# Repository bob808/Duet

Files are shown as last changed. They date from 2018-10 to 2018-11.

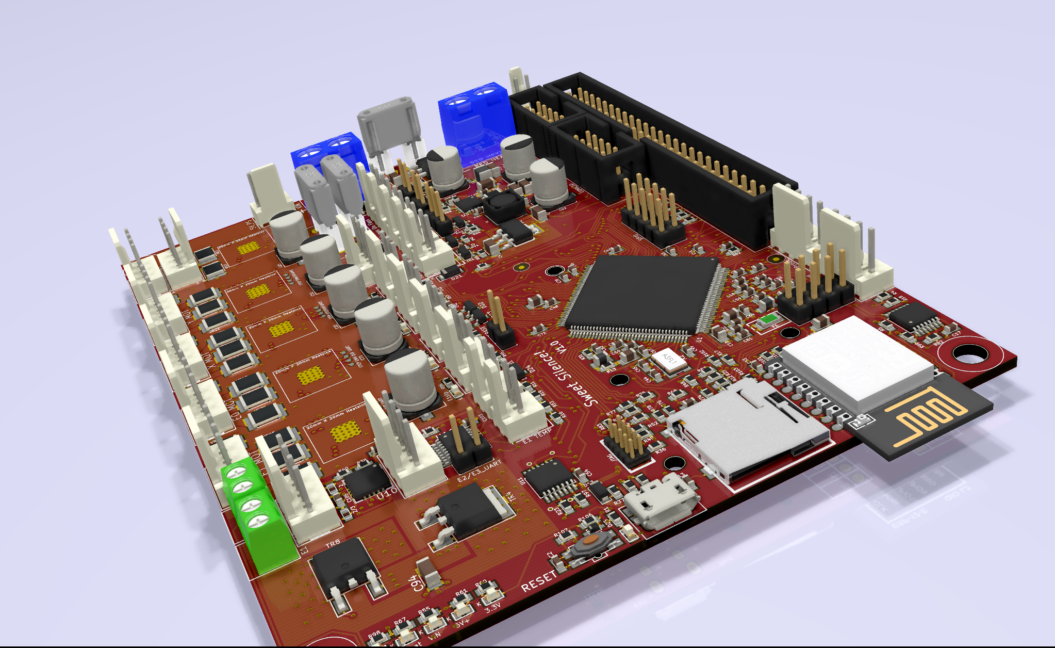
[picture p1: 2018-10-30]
top w:o radiators.png

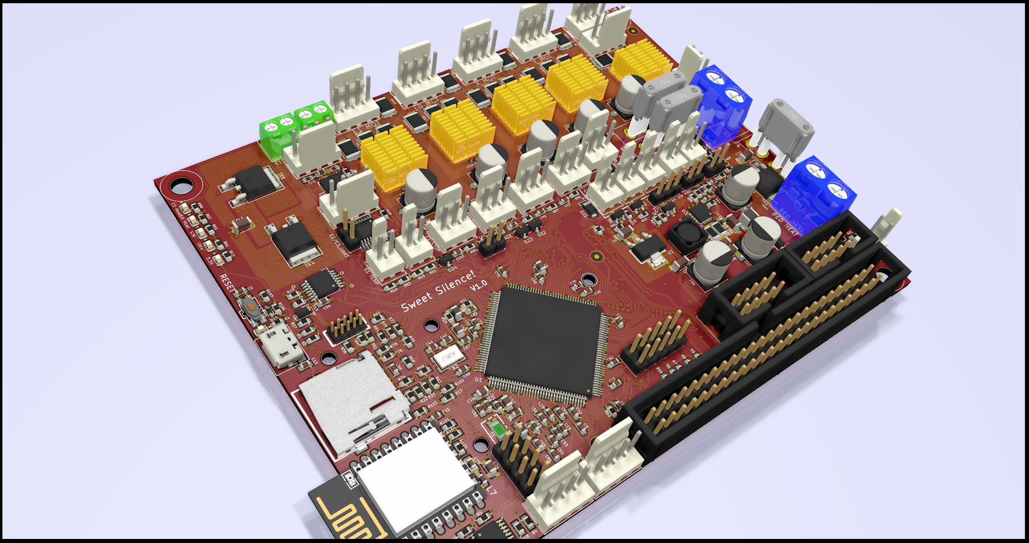
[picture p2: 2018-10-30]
top with radiators.png

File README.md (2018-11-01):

# The Sweet Silence! 3D Printer Controller design files repository.

Sweeet Silence is a Duet2 Wifi spinoff, using tmc2228 drivers, mounted on the back of the pcb for better 
cooling (heatsinks on top pf pcb). Uses the same ATSAM4E8E processor. Output stage has been completely redone,
and includes full protection suite from the datasheet (ferrite beads/varistors and caps on BRA/BRB).
You can skip the varistors, drivers work fine without them.
There's 2x MAX31865 chips on board, you can use it directly with PT100/1000 sensors. There's also options
for 4/3/2 wire setups.
The driver control should be the same from Maestro.
There's E2/E3 extra UART connections for external drivers.
Few pins from 2x25 header are different, and debugging led is gone. Everything else should be the same.

Will update later on with more details. I found all parts at TME/Farnell. 
Firmware needs to be modified to account for correct pin numbers.
Ah, and max31865 is to be bitbanged. No hardware SPI in that area.

The recommended firmware is DC42's branch of the RepRapFirmware:
https://github.com/dc42/RepRapFirmware

Based on :
Duet 2 Wifi 
Design by Tony Lock and David Crocker
More info:
https://www.duet3d.com/
LICENSE: see the LICENSE file in the repository

Developed in KiCAD: http://www.kicad-pcb.org/display/KICAD/KiCad+EDA+Software+Suite

top with radiators
top w o radiators
bottom

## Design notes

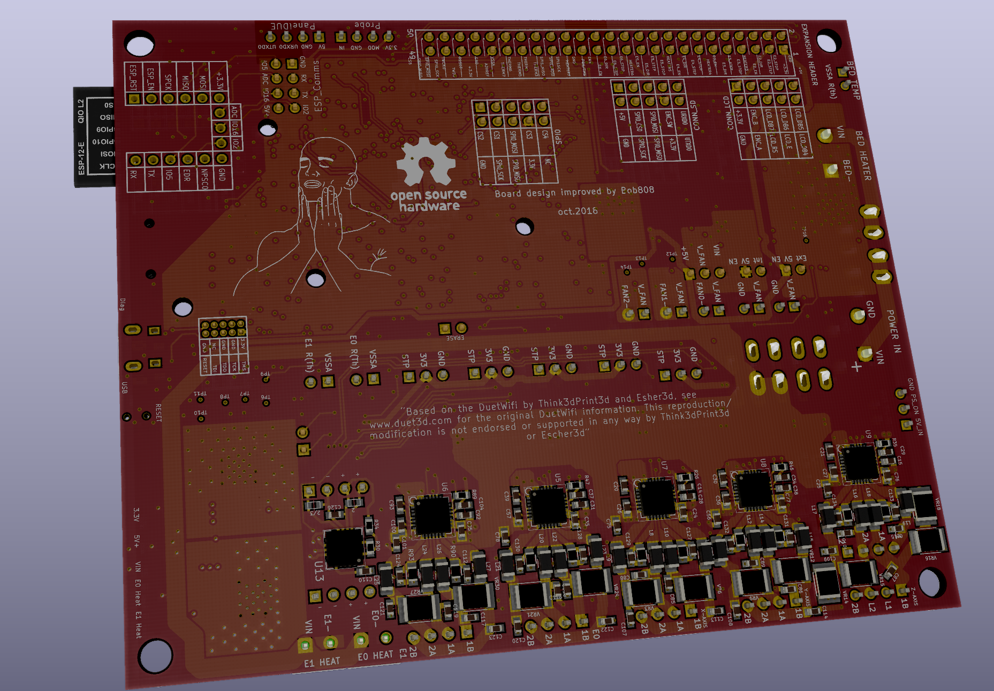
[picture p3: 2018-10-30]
bottom.png

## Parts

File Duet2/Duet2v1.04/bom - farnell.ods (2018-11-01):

Order Code | Quantity | Mfg. Code | Mfg Name | Description
2515574 | 2 | MAX31865ATP+ | MAXIM INTEGRATED PRODUCTS | MAXIM INTEGRATED PRODUCTS Temperature Sensor IC, RTD, Digital, ± 0.5°C, -40 °C, 125 °C, TQFN, 20 Pins
1669752 | 10 | MPZ2012S221A | TDK | TDK Ferrite Bead, 0805 [2012 Metric], 220 ohm, 3 A, MPZ Series, 0.04 ohm, ± 25%
2822172 | 5 | TMC2224-LA-T | TRINAMIC | TRINAMIC Motor Driver/Controller, Stepper, UART, 1 Output, 4.75 V to 36 V Supply, 1.4 A Out, QFN-28
2496341 | 1 | SN74CB3Q3251PWR | TEXAS INSTRUMENTS | TEXAS INSTRUMENTS Multiplexer / Demultiplexer Bus Switch, CB3Q Family, 1 Channels, 1:8, 2.3 V to 3.6 V, TSSOP-16
7261403 | 1 | TS2940CW-3.3 RP | TAIWAN SEMICONDUCTOR | TAIWAN SEMICONDUCTOR Fixed LDO Voltage Regulator, 0V to 35V, 600mV Dropout, 3.3Vout, 1Aout, SOT-223-3
2292371 | 20 | HI1206T500R-10 | LAIRD | LAIRD Ferrite Bead, 1206 [3216 Metric], 50 ohm, 6 A, HI Series, 0.01 ohm
2292537 | 1 | TYS6045100M-10 | LAIRD | LAIRD Power Inductor (SMD), 10 µH, 2.45 A, Shielded, 3.2 A, TYS Series, 6mm x 6mm x 4.5mm
2534550 | 1 | 74479299210 | WURTH ELEKTRONIK | WURTH ELEKTRONIK Power Inductor (SMD), 1 µH, Shielded, 5.2 A, WE-PMCI Series, 1210 [3225 Metric]
2834883 | 1 | 0ZCJ0020FF2E | BEL FUSE - CIRCUIT PROTECTION | BEL FUSE - CIRCUIT PROTECTION PPTC Resettable Fuse, SMD, 0ZCJ Series, 200 mA, 400 mA, 30 VDC, -40 °C
2889217 | 5 | SL04-HE3-08 | VISHAY | VISHAY Schottky Rectifier, 40 V, 1.1 A, Single, DO-219AB, 2 Pins, 540 mV
2504957 | 3 | ACPP06034K7BE | ARCOL | ARCOL SMD Chip Resistor, Precision Passivated, 4.7 kohm, ACPP Series, 50 V, Thin Film, 0603 [1608 Metric]
2861442 | 10 | CRGCQ0603F27R | TE CONNECTIVITY | TE CONNECTIVITY SMD Chip Resistor, 27 ohm, CRGCQ Series, 75 V, Thick Film, 0603 [1608 Metric], 100 mW
1081192 | 5 | BAT54C,215 | NEXPERIA | NEXPERIA Small Signal Schottky Diode, Dual Common Cathode, 30 V, 200 mA, 800 mV, 600 mA, 150 °C
2116426 | 10 | RLP73K2BR12JTD | TE CONNECTIVITY | TE CONNECTIVITY SMD Current Sense Resistor, 0.12 ohm, RL73 Series, 1206 [3216 Metric], 500 mW, ± 5%, Thick Film
2908248 | 30 | CR0603-FX-1002GLF | BOURNS | BOURNS SMD Chip Resistor, 10 kohm, CR Series, 50 V, Thick Film, 0603 [1608 Metric], 100 mW
2861477 | 10 | CRGCQ0603F22K | TE CONNECTIVITY | TE CONNECTIVITY SMD Chip Resistor, 22 kohm, CRGCQ Series, 75 V, Thick Film, 0603 [1608 Metric], 100 mW
2074166 | 10 | MCSR06X1001FTL | MULTICOMP | MULTICOMP SMD Chip Resistor, 1 kohm, MCSR 06 Series, 75 V, Ceramic, 0603 [1608 Metric], 100 mW
2447363 | 10 | MCWR06X3901FTL | MULTICOMP | MULTICOMP SMD Chip Resistor, 3.9 kohm, MCWR Series, 50 V, Thick Film, 0603 [1608 Metric], 100 mW
2861497 | 10 | CRGCQ0603F1M0 | TE CONNECTIVITY | TE CONNECTIVITY SMD Chip Resistor, 1 Mohm, CRGCQ Series, 75 V, Thick Film, 0603 [1608 Metric], 100 mW
2496924 | 20 | 0603X225K6R3CT | WALSIN | WALSIN SMD Multilayer Ceramic Capacitor, 2.2 µF, 6.3 V, 0603 [1608 Metric], ± 10%, X5R
2896440 | 10 | VJ0603Y223KXACW1BC | VISHAY | VISHAY SMD Multilayer Ceramic Capacitor, 22000 pF, 50 V, 0603 [1608 Metric], ± 10%, X7R, VJ Series
2896419 | 10 | VJ0603Y103KXAPW1BC | VISHAY | VISHAY SMD Multilayer Ceramic Capacitor, 10000 pF, 50 V, 0603 [1608 Metric], ± 10%, X7R, VJ Series
2362105 | 5 | GRM21BR60J106KE01L | MURATA | MURATA SMD Multilayer Ceramic Capacitor, 10 µF, 6.3 V, 0805 [2012 Metric], ± 10%, X5R, GRM Series
2112852 | 5 | LMK212B7475KG-T | TAIYO YUDEN | TAIYO YUDEN SMD Multilayer Ceramic Capacitor, 4.7 µF, 10 V, 0805 [2012 Metric], ± 10%, X7R, M Series
2611949 | 10 | GRM319R6YA106KA12D | MURATA | MURATA SMD Multilayer Ceramic Capacitor, 10 µF, 35 V, 1206 [3216 Metric], ± 10%, X5R, GRM Series
1868417 | 7 | EEEFT1V101AP | PANASONIC ELECTRONIC COMPONENTS | PANASONIC ELECTRONIC COMPONENTS SMD Aluminium Electrolytic Capacitor, Radial Can - SMD, 100 µF, 35 V, 0.26 ohm, FT Series
2861485 | 10 | CRGCQ0603F100K | TE CONNECTIVITY | TE CONNECTIVITY SMD Chip Resistor, 100 kohm, CRGCQ Series, 75 V, Thick Film, 0603 [1608 Metric], 100 mW
2447385 | 10 | MCWR06X4701FTL | MULTICOMP | MULTICOMP SMD Chip Resistor, 4.7 kohm, MCWR Series, 50 V, Thick Film, 0603 [1608 Metric], 100 mW
2078911 | 10 | ASC0603-2K2FT5 | TT ELECTRONICS / WELWYN | TT ELECTRONICS / WELWYN SMD Chip Resistor, 2.2 kohm, ASC Series, 50 V, Thick Film, 0603 [1608 Metric], 100 mW
2074202 | 10 | MCSR06X1800FTL | MULTICOMP | MULTICOMP SMD Chip Resistor, 180 ohm, MCSR 06 Series, 75 V, Ceramic, 0603 [1608 Metric], 100 mW
2447419 | 10 | MCWR06X6800FTL | MULTICOMP | MULTICOMP SMD Chip Resistor, 680 ohm, MCWR Series, 50 V, Thick Film, 0603 [1608 Metric], 100 mW
2447362 | 10 | MCWR06X3601FTL | MULTICOMP | MULTICOMP SMD Chip Resistor, 3.6 kohm, MCWR Series, 50 V, Thick Film, 0603 [1608 Metric], 100 mW
2861481 | 10 | CRGCQ0603F47K | TE CONNECTIVITY | TE CONNECTIVITY SMD Chip Resistor, 47 kohm, CRGCQ Series, 75 V, Thick Film, 0603 [1608 Metric], 100 mW
2447227 | 10 | MCWR06X1000FTL | MULTICOMP | MULTICOMP SMD Chip Resistor, 100 ohm, MCWR Series, 50 V, Thick Film, 0603 [1608 Metric], 100 mW
2447298 | 10 | MCWR06X2200FTL | MULTICOMP | MULTICOMP SMD Chip Resistor, 220 ohm, MCWR Series, 50 V, Thick Film, 0603 [1608 Metric], 100 mW
2078905 | 10 | ASC0603-470RFT5 | TT ELECTRONICS / WELWYN | TT ELECTRONICS / WELWYN SMD Chip Resistor, 470 ohm, ASC Series, 50 V, Thick Film, 0603 [1608 Metric], 100 mW
2073453 | 10 | MCMR06X2702FTL | MULTICOMP | MULTICOMP SMD Chip Resistor, Ceramic, 27 kohm, MCMR Series, 75 V, Thick Film, 0603 [1608 Metric], 100 mW
2861445 | 10 | CRGCQ0603F47R | TE CONNECTIVITY | TE CONNECTIVITY SMD Chip Resistor, 47 ohm, CRGCQ Series, 75 V, Thick Film, 0603 [1608 Metric], 100 mW
2078888 | 10 | ASC0603-1R0FT5 | TT ELECTRONICS / WELWYN | TT ELECTRONICS / WELWYN SMD Chip Resistor, 1 ohm, ASC Series, 50 V, Thick Film, 0603 [1608 Metric], 100 mW
2812361 | 20 | 885012206106 | WURTH ELEKTRONIK | WURTH ELEKTRONIK SMD Multilayer Ceramic Capacitor, 470 pF, 100 V, 0603 [1608 Metric], ± 10%, X7R, WCAP-CSGP Series
2896437 | 10 | VJ0603Y222JXACW1BC | VISHAY | VISHAY SMD Multilayer Ceramic Capacitor, 2200 pF, 50 V, 0603 [1608 Metric], ± 5%, X7R, VJ Series
2896423 | 60 | VJ0603Y104JXACW1BC | VISHAY | VISHAY SMD Multilayer Ceramic Capacitor, 0.1 µF, 50 V, 0603 [1608 Metric], ± 5%, X7R, VJ Series
2066899 | 2 | 744760410A | WURTH ELEKTRONIK | WURTH ELEKTRONIK Surface Mount High Frequency Inductor, WE-RFI Series, 10 µH, 80 mA, 0805 [2012 Metric], Wirewound
1675756 | 50 | MC34485 | MULTICOMP | MULTICOMP Connector Housing, MC34 Series, Receptacle, 4 Ways, 2.54 mm, 2218T Crimp Contacts, Yes
1675755 | 50 | MC34483 | MULTICOMP | MULTICOMP Connector Housing, MC34 Series, Receptacle, 3 Ways, 2.54 mm, 2218T Crimp Contacts, Yes
1675754 | 50 | MC34481 | MULTICOMP | MULTICOMP Connector Housing, MC34 Series, Receptacle, 2 Ways, 2.54 mm, 2218T Crimp Contacts, Yes
1675764 | 50 | MC34629 | MULTICOMP | MULTICOMP Wire-To-Board Connector, Vertical, 2.54 mm, 2 Contacts, Header, MC34 Series, Through Hole, 1 Rows
1860642 | 100 | MC346772 | MULTICOMP | MULTICOMP Contact, Socket, Crimp, 18 AWG, Tin Plated Contacts, Multicomp's 4.2mm Housings
1748753 | 1 | 744761047C | WURTH ELEKTRONIK | WURTH ELEKTRONIK Surface Mount High Frequency Inductor, WE-KI Series, 4.7 nH, 700 mA, 0603 [1608 Metric], Wirewound
2554980 | 1 | ZX62D-B-5P8(30) | HIROSE(HRS) | HIROSE(HRS) USB Connector, Micro USB Type B, USB 2.0, Receptacle, 5 Ways, Surface Mount, Through Hole Mount
2696554 | 10 | UCR10EVHFSR075 | ROHM | ROHM SMD Current Sense Resistor, 0.075 ohm, UCR Series, 0805 [2012 Metric], 330 mW, ± 1%, Thick Film

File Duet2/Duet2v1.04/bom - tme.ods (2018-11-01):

Symbol | Manufacturer part number | Producer | Quantity
PMV40UN2R | PMV40UN2R | NEXPERIA | 5
ZL231-50PG | DS1013-50SSIB1 | CONNFLY | 1
DS1017-01-10NA8 | DS1017-01-10NA8 | CONNFLY | 1
IPD040N03LGATMA1 | IPD040N03LGATMA1 | INFINEON TECHNOLOGIES | 5
UCV1V221MCL1GS | UCV1V221MCL1GS | NICHICON | 1
A4403GEUTR-T | A4403GEUTR-T | ALLEGRO MICROSYSTEMS | 1
SN74HC74PW | SN74HC74PW | TEXAS INSTRUMENTS | 3
SN74HCT02PW | SN74HCT02PW | TEXAS INSTRUMENTS | 3
ATSAM4E8EA-AN | ATSAM4E8EA-AN | MICROCHIP TECHNOLOGY | 1
KEYS3522 | 3522 | KEYSTONE | 10
0ZCJ0020FF2E | 0ZCJ0020FF2E | BEL FUSE | 1
B72580V250K62 | B72580V250K62 | EPCOS | 30
MCC-SDMICRO/3 | 112J-TDAR-R01 | ATTEND | 1
MX-105017-0001 | 105017-0001 | MOLEX | 2
KMR223GLFG | Y78B22310FP | C&K | 1
KMS233GLFG | Y28B23310FP | C&K | 1
20021111-00010T4LF | 20021111-00010T4LF | AMPHENOL | 2
MKDS5/2-6.35 | MKDS 5/ 2-6 | 35 1714955 PHOENIX CONTACT | 2
TB-3.5-P-2P-GY | TB-3.5-P-2P-GY | NINIGI | 2
NS25-W3P | NS25-W3P | NINIGI | 10
MX-22-23-2041 | 22-23-2041 | MOLEX | 10
OSR50603C1E | OSR50603C1E | OPTOSUPPLY | 10
OSO50603C1E | OSO50603C1E | OPTOSUPPLY | 10
OSG80603C1E | OSG80603C1E | OPTOSUPPLY | 10
RB751S40.115 | RB751S40.115 | NEXPERIA | 10
SS14M | SS14M RS | TAIWAN SEMICONDUCTOR | 5
SKL33-DIO | SKL33 | DIOTEC SEMICONDUCTOR | 5
OSM50603C1E | OSM50603C1E | OPTOSUPPLY | 5
1-826632-0 | 1-826632-0 | TE CONNECTIVITY | 1
826629-6 | 826629-6 | TE CONNECTIVITY | 3
75869-301LF | 75869-301LF | AMPHENOL | 2
ISM92-3351AH12.00 | ISM92-3351AH-12.0000 | ILSI | 1

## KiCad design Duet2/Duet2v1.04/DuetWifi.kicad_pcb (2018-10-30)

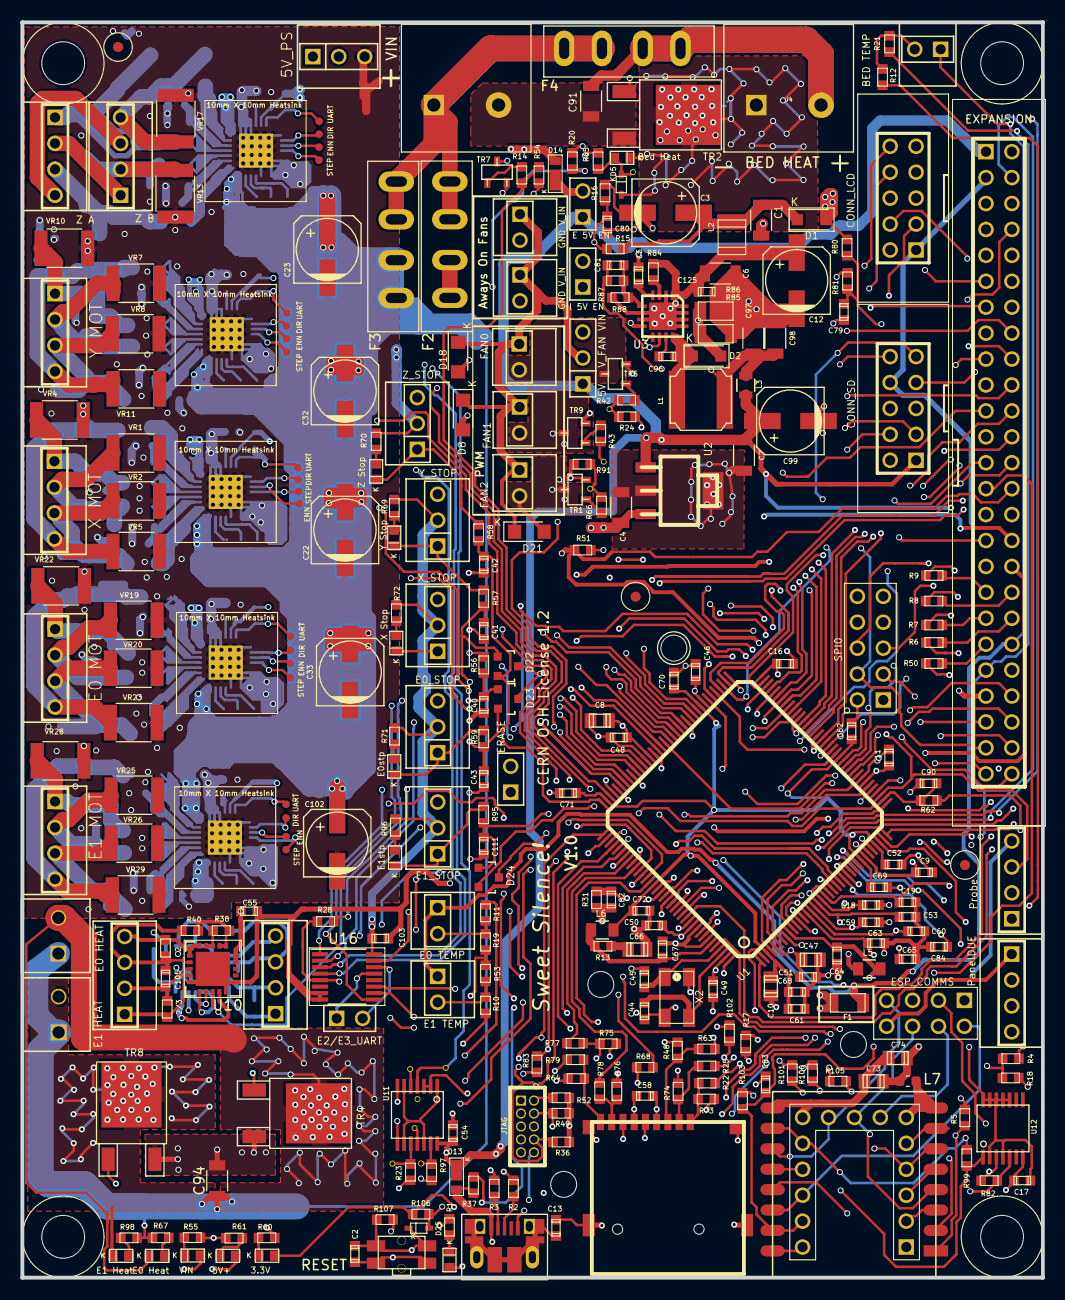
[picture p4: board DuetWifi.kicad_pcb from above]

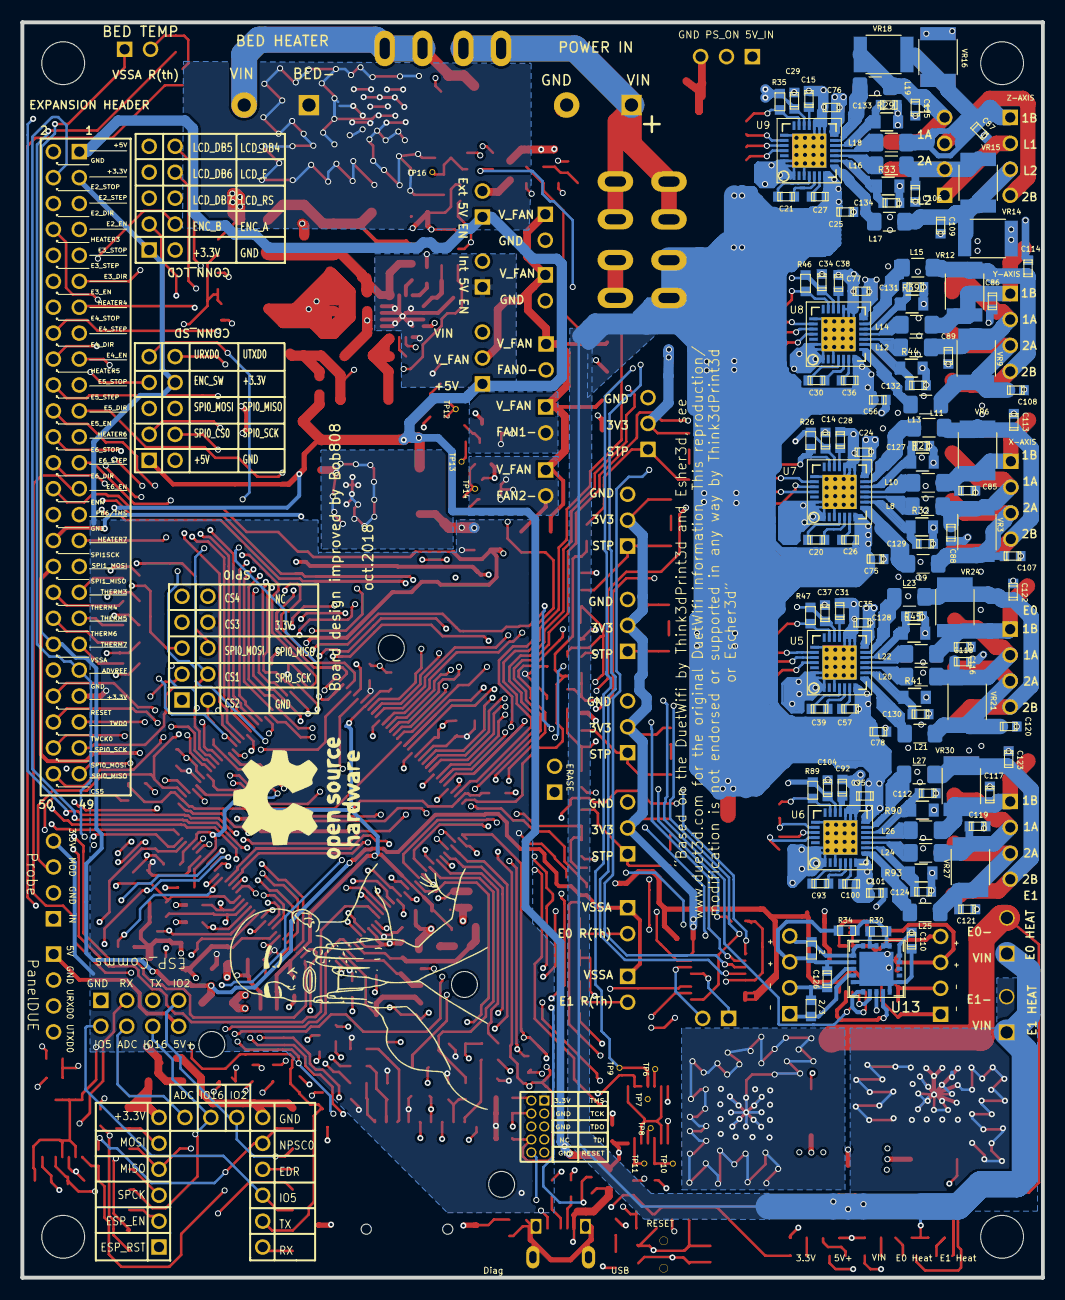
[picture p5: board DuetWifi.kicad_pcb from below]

Board: 4 copper layers, 100.0 x 123.0 mm, 430 parts (120 on the bottom side), 305 nets.

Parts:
C1, C4, C6, C7, C91, C94, C97, C98: 10u 35V; C_1206
C2, C13, C79, C80, C81: 0u01; C_0603
C3, C12, C22, C23, C32, C33, C102: 100u 35V; C_ELEC_6.3x7.7
C5, C9, C11, C16, C17, C29, C34, C37, C46, C48, C49, C50, C51, C52, C54, C61, C62, C64, C67, C69, C70, C71, C72, C82, C103, C104: 0u1; C_0603
C8, C10, C47, C73, C74: 10u; C_0805
C14, C24, C25, C35, C56, C75, C76, C77, C78, C95, C101: 0u1 50V; C_0603
C15, C18, C19, C28, C31, C38, C53, C58, C59, C60, C63, C65, C68, C84, C92: 2u2; C_0603
C20, C21, C30, C39, C93: 22n X7R 10% 16V; C_0603
C26, C27, C36, C57, C100: 0.1u 50V; C_0603
C40, C41, C42, C43, C55, C90, C110, C111: 2n2; C_0603
C44, C45: 10p; C_0603
C66: 4u7; C_0805
C83: DNP 47p; C_0603
C85, C86, C87, C88, C89, C106, C107, C108, C109, C113, C114, C115, C116, C117, C118, C119, C120, C121, C122, C123: 470p 100V; C_0603
C96: 22nF; C_0603
C99: 220u 25V; C_ELEC_6.3x7.7
C105, C126: 10n/100n; C_0603
C112, C124, C127, C128, C129, C130, C131, C132, C133, C134: 0u1 16V; C_0603
C125: 0u1 35V; C_0603
D1, D2: DB2W40300L; D_SOD-123F
D3: USB; D_0603
D5, D25: SOD-523F
D6: Bed Heat; D_0603
D7: E0 Heat; D_0603
D8, D18, D21: DO-219AB
D9: Y Stop; D_0603
D10: Z Stop; D_0603
D11: E0stp; D_0603
D12: X Stop; D_0603
D13, D14: SS14M; uSMA
D15: VIN; D_0603
D16: 3.3V; D_0603
D17: 5V+; D_0603
D19: E1stp; D_0603
D20: E1 Heat; D_0603
D22, D23, D24: BAT54C; SOT-23-D
F1: PPTC Resettable Fuse; R_1206
F2: FAN FUSE; MCCQ-122-minibladefuseholder
F3: EXT/STEP FUSE; MCCQ-122-minibladefuseholder
F4: BED FUSE; MCCQ-122-minibladefuseholder
J1: EXPANSION; PIN_ARRAY_25X2
J2: FAN2; PIN_ARRAY_2X1
J3: 5V V_FAN VIN; CONN_3x1
J4: BED HEAT; TERM_2-WAY_6.35mm
J5: BED TEMP; PIN_ARRAY_2X1
J6: E1 MOT; PIN_ARRAY_4x1
J7: Z B; PIN_ARRAY_4x1
J8: Y MOT; PIN_ARRAY_4x1
J9: X MOT; PIN_ARRAY_4x1
J10: E0 MOT; PIN_ARRAY_4x1
J11: E0 HEAT; 3.5MM_2X1
J12: E0 TEMP; PIN_ARRAY_2X1
J13: E1 HEAT; 3.5MM_2X1
J14: E1 TEMP; PIN_ARRAY_2X1
J15: uSDHC; uSD_SKT
J16: CONN_ALT_HEADER
J17, J18: + + - -; PIN_ARRAY_4x1
J19: Z_STOP; PIN_ARRAY_3X1
J20: 5V_PS; PIN_ARRAY_3X1
J21: JTAG; MICRO_5x2
J22: USB; uUSB_new
J23: VIN; TERM_2-WAY_6.35mm
J24, J31: GND V_IN; PIN_ARRAY_2X1
J25: FAN0; PIN_ARRAY_2X1
J26: E2/E3_UART; PIN_ARRAY_2X1_mod
J27, J42, J46, J50, J54: UART; tp_smd
J28: Probe; PIN_ARRAY_4x1
J29: FAN1; PIN_ARRAY_2X1
J30: PanelDUE; PIN_ARRAY_4x1
J32: Y_STOP; PIN_ARRAY_3X1
J33: X_STOP; PIN_ARRAY_3X1
J34: E0_STOP; PIN_ARRAY_3X1
J35: E1_STOP; PIN_ARRAY_3X1
J36: Z A; PIN_ARRAY_4x1
J37: SPI0; MAX_TEMP_DB
J38, J43, J47, J51, J55: ENN; tp_smd
J39: ESP_COMMS; CONN_4x2
J40, J44, J48, J52, J56: DIR; tp_smd
J41, J45, J49, J53, J57: STEP; tp_smd
JP1: ERASE; JUMPER
JP9: I 5V EN; JUMPER
JP10: E 5V EN; JUMPER
Ju1, Ju4: 2; R_0603
Ju2, Ju3: 2/3; R_0603
L1: 10uH; L_6x6
L2: 1uH; C_1210
L3: 220 ohm, 3 A; R_0805
L5, L6: 10uH 100Mhz; R_0805_extended_pads
L7: 4n7h; L_0603_1608Metric
L8, L10, L11: 50R@100MHz; L_1206_3216Metric_Pad1.42x1.75mm_HandSolder
L9, L12, L13, L14, L15, L16, L17, L18, L19, L20, L21, L22, L23, L24, L25, L26, L27: 50R@100MHz; R_1206_3216Metric_Pad1.42x1.75mm_HandSolder
M1, M2, M3: FID; Fiducial_1mm_Dia_2.54mm_Outer_CopperTop
M4, M5, M6, M7: MOUNTING; Fixing_M4
M8: LOGO; LOGO1
M11: LOGO; Untitled
P1: CONN_SD; IDC_PIN_ARRAY_5x2
P2: CONN_LCD; IDC_PIN_ARRAY_5x2
R1, R4, R17, R61, R99, R102: 2K2; R_0603
R2, R3: 27R 1%; R_0603
R5, R103: 470R; R_0603
R6, R7, R8, R9, R10, R11, R12, R24, R50, R51, R56, R57, R58, R59, R62, R63, R64, R83, R91, R95, R106: 10K; R_0603
R13: 1R; R_0603
R14, R28, R42, R43, R66, R69, R70, R71, R72, R96: 1K; R_0603
R15, R80: 47K 1%; R_0603
R16, R81: 4K7 1%; R_0603
R18, R54, R55, R65, R67, R98: 4K7; R_0603
R19, R21, R53: 4K7 0.1%; R_0603
R20, R23, R60, R97: 180R; R_0603
R22, R25, R48, R77, R78, R79: 220R; R_0603
R26, R35, R46, R47, R89: 22K; R_0603
R27, R29, R32, R33, R39, R41, R44, R45, R90, R93: 0R075 1% 0.33W; R_0805_extended_pads
R30, R38: 3k9; R_0603
R31: 47K; R_0603
R34, R40: 10M; R_0603
R36, R49, R52: DNP 100K; R_0603
R37: 27K; R_0603
R68, R107: 100R; R_0603
R73, R74, R75, R76: DNP 47K; R_0603
R82: 0R DNP; R_0603
R84: 100K; R_0603
R85, R86: 0R13 0.33W; R_1206
R87: 3K6; R_0603
R88: 680R; R_0603
R100, R101, R105: 47R; R_0603
S1: RESET; SW_SIDE_1_lugs
TP6, TP7, TP8, TP9, TP10, TP11, TP12, TP13, TP14, TP16: TP; TP_via
TR1, TR5, TR7, TR9: PMV40UN2; SOT-23
TR2, TR4, TR8: IPD036N04L; D-PAK
U1: ATSAM4E8E; LQFP144
U2: AP7361C-33E-13; SOT-223
U3: A4403; QFN16-4x4
U4: ESP-07/12; ESP-12S
U5, U6, U7, U8, U9: TMC2224; QFN-28-1EP_5x5mm_Pitch0.5mm
U10, U13: MAX31865AAP(SSOP20); QFN-20-1EP_5x5mm_Pitch0.65mm_mod
U11: 74HCT02; TSSOP-14
U12: 74HC74; TSSOP-14
U16: SN74CB3Q3251; QSOP-16_3.9x4.9mm_Pitch0.635mm
VR1, VR2, VR3, VR4, VR5, VR6, VR7, VR8, VR9, VR10, VR11, VR12, VR13, VR14, VR15, VR16, VR17, VR18, VR19, VR20, VR21, VR22, VR23, VR24, VR25, VR26, VR27, VR28, VR29, VR30: 3J; L_1812_HandSoldering
X2: CRYSTAL_4PIN; Xtal_5x3.2

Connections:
5V_IN: D14.1, J20.1
+3.3V: C4.1, C8.1, C9.1, C11.1, C14.1, C16.1, C17.1, C29.1, C34.1, C37.1, C46.1, C47.1, C48.1, C49.1, C50.1, C51.1, C55.1, C58.1, C73.1, C74.1, C103.2, C104.1, C110.1, D16.1, D22.3, D23.3, D24.3, J1.3, J1.43, J15.4, J19.2, J21.1, J28.4, J32.2, J33.2, J34.2, J35.2, J37.8, JP1.1, L5.2, L7.1, P1.8, P2.1, R26.2, R35.2, R36.1, R46.2, R47.2, R49.1, R51.1, R52.1, R63.2, R64.2, R69.2, R70.2, R71.2, R72.2, R73.2, R74.2, R75.2, R76.2, R89.1, R96.2, R106.2, U1.5, U1.30, U1.43, U1.72, U1.80, U1.96, U1.134, U1.143, U2.3, U5.19, U6.19, U7.19, U8.19, U9.19, U10.19, U10.20, U11.2, U11.3, U12.2, U12.4, U12.10, U12.11, U12.12, U12.13, U12.14, U13.19, U13.20, U16.16
+5V: C7.1, C54.1, C99.1, D13.2, D17.1, J1.1, J1.33, J3.1, J30.1, J39.8, JP10.1, L3.1, P1.1, U2.1, U11.14
/Processor/VDDCORE: C10.1, C52.1, C61.1, C62.1, C68.1, C69.1, C70.1, C71.1, C72.1, L6.1, U1.3, U1.29, U1.33, U1.50, U1.81, U1.107, U1.123
ADC: J16.7, J39.4, U4.2
ADVREF: C64.1, J1.41, L5.1, R19.2, R21.2, R53.2, U1.9
BED-: D5.2, D6.2, J4.1, TR2.D
BED_PWM: R20.2, TP9.1, U11.4
CS3: J37.7, U1.117
CS4: J37.9, U1.120
CS5: J1.50, U1.56
D6_TestPoint: D5.1, D6.1, R65.1, TP16.1
DDM: R3.2, U1.136
DDP: R2.2, U1.137
E0-: D7.2, J11.2, TR4.D
E0_DIR: J52.1, U1.99, U5.23
E0_MOT_1A: C118.1, J10.2, L20.1, VR19.1, VR21.1
E0_MOT_1B: C116.1, J10.1, L22.1, VR22.1, VR24.1
E0_MOT_2A: C120.2, J10.3, L21.1, VR20.2, VR21.2
E0_MOT_2B: C122.2, J10.4, L23.1, VR23.2, VR24.2
E0_PWM: R23.2, TP10.1, U11.10
E0_STEP: J53.1, U1.125, U5.25
E0_STOP: C43.1, D23.2, R59.1, U1.101
E0_STOP_CONN: D11.2, J34.1, R59.2
E0_UART: J50.1, R47.1, U5.20, U16.1
E1-: D20.2, J13.2, TR8.D
E1_DIR: J56.1, U1.110, U6.23
E1_MOT_1A: C119.1, J6.2, L24.1, VR25.1, VR27.1
E1_MOT_1B: C117.1, J6.1, L26.1, VR28.1, VR30.1
E1_MOT_2A: C121.2, J6.3, L25.1, VR26.2, VR27.2
E1_MOT_2B: C123.2, J6.4, L27.1, VR29.2, VR30.2
E1_PWM: R97.2, TP11.1, U11.13
E1_STEP: J57.1, U1.126, U6.25
E1_STOP: C111.1, D24.1, R95.1, U1.100
E1_STOP_CONN: D19.2, J35.1, R95.2
E1_UART: J54.1, R89.2, U6.20, U16.15
E2_DIR: J1.6, U1.71
E2_EN: J1.7, U1.57
E2_STEP: J1.5, U1.131
E2_STOP: J1.4, U1.4
E2_UART: J26.2, U16.14
E3_DIR: J1.11, U1.60
E3_EN: J1.12, U1.55
E3_STEP: J1.10, U1.132
E3_STOP: J1.9, U1.6
E3_UART: J26.1, U16.13
E4_DIR: J1.16, U1.78
E4_EN: J1.17, U1.52
E4_STEP: J1.15, U1.1
E4_STOP: J1.14, U1.7
E5_DIR: J1.21, U1.74
E5_EN: J1.22, U1.53
E5_STEP: J1.20, U1.128
E5_STOP: J1.19, U1.10
E6_DIR: J1.26, U1.11
E6_EN: J1.27, U1.140
E6_STEP: J1.25, U1.47
E6_STOP: J1.24, U1.25
EDR_CONN: J16.12, R17.1, U4.12
ENC_A: P2.4, U1.36
ENC_B: P2.3, U1.48
ENC_SW: P1.7, U1.35
ENN: J1.28, J38.1, J43.1, J47.1, J51.1, J55.1, R51.2, U1.54, U5.24, U6.24, U7.24, U8.24, U9.24
ERASE: JP1.2, U1.87
ESP_3.3VIN: J16.6, L7.2, U4.8
ESP_DATA_RDY: R17.2, U1.2
ESP_EN: J16.2, R18.1, U1.28, U4.3
ESP_RST: J16.1, R5.2, U1.27
FAN0: R24.2, R42.2, TP12.1, U1.127
FAN0-: D18.2, J25.2, TR5.D
FAN1: R43.2, TP13.1, U1.13
FAN1-: D8.2, J29.2, TR9.D
FAN2: R66.2, R91.2, TP14.1, U1.102
FAN2-: D21.2, J2.2, TR1.D
GND: C1.2, C2.2, C3.2, C4.2, C5.2, C6.2, C7.2, C8.2, C9.2, C10.2, C11.2, C12.2, C13.2, C14.2, C15.2, C16.2, C17.2, C18.2, C19.2, C22.2, C23.2, C24.2, C25.2, C28.2, C29.2, C31.1, C32.2, C33.2, C34.2, C35.2, C37.2, C38.2, C40.2, C41.2, C42.2, C43.2, C44.2, C45.2, C46.2, C47.2, C48.2, C49.2, C50.2, C51.2, C52.2, C53.2, C54.2, C55.2, C56.2, C58.2, C59.2, C60.2, C61.2, C62.2, C63.2, C64.2, C65.2, C66.2, C67.2, C68.2, C69.2, C70.2, C71.2, C72.2, C73.2, C74.2, C75.2, C76.2, C77.2, C78.2, C79.2, C80.2, C82.2, C83.2, C84.2, C85.1, C86.1, C87.1, C88.1, C89.1, C90.2, C91.2, C92.2, C94.2, C95.2, C97.2, C98.2, C99.2, C101.2, C102.2, C103.1, C104.2, C106.1, C107.2, C108.2, C109.2, C110.2, C111.2, C112.1, C113.2, C114.2, C115.2, C116.2, C117.2, C118.2, C119.2, C120.1, C121.1, C122.1, C123.1, C124.1, C125.2, C127.1, C128.1, C129.1, C130.1, C131.1, C132.1, C133.1, C134.1, F1.2, J1.2, J1.30, J1.42, J15.6, J15.G, J16.10, J19.3, J20.3, J21.3, J21.5, J21.9, J22.5, J23.2, J24.2, J28.2, J30.2, J31.2, J32.3, J33.3, J34.3, J35.3, J37.2, J39.1, JP9.1, P1.2, P2.2, R1.2, R4.2, R16.2, R18.2, R24.1, R27.1, R29.1, R31.2, R32.1, R33.1, R39.1, R41.1, R44.1, R45.1, R54.2, R55.2, R60.2, R61.2, R81.2, R85.1, R86.1, R88.2, R90.2, R91.1, R93.2, S1.1, S1.2, TR1.S, TR2.S, TR4.S, TR5.S, TR7.S, TR8.S, TR9.S, U1.8, U1.44, U1.61, U1.85, U1.95, U1.104, U1.115, U1.135, U1.138, U2.2, U2.4, U3.2, U3.6, U3.7, U3.9, U3.13, U3.14, U3.15, U3.16, U3.17, U4.9, U5.1, U5.3, U5.15, U5.16, U5.17, U5.22, U5.27, U5.28, U5.29, U6.1, U6.3, U6.15, U6.16, U6.17, U6.22, U6.27, U6.28, U6.29, U7.1, U7.3, U7.15, U7.16, U7.17, U7.22, U7.27, U7.28, U7.29, U8.1, U8.3, U8.15, U8.16, U8.17, U8.22, U8.27, U8.28, U8.29, U9.1, U9.3, U9.15, U9.16, U9.17, U9.22, U9.27, U9.28, U9.29, U10.10, U10.15, U10.16, U10.21, U11.7, U12.7, U13.10, U13.15, U13.16, U13.21, U16.7, U16.8, VR1.2, VR2.1, VR4.2, VR5.1, VR7.2, VR8.1, VR10.2, VR11.1, VR13.2, VR14.1, VR16.2, VR17.1, VR19.2, VR20.1, VR22.2, VR23.1, VR25.2, VR26.1, VR28.2, VR29.1, X2.2, X2.4
GPIO2: J16.9, J39.7, U4.11
GPIO5: J16.13, J39.2, U4.14
GPIO16: J16.8, J39.6, U4.4
HEATER0: TP6.1, U1.23, U11.5
HEATER1: TP7.1, U1.22, U11.8
HEATER2: TP8.1, U1.45, U11.11
HEATER3: J1.8, U1.40
HEATER4: J1.13, U1.58
HEATER5: J1.18, U1.82
HEATER6: J1.23, U1.94
HEATER7: J1.31, U1.49
LCD_DB4: P2.10, U1.63
LCD_DB5: P2.9, U1.65
LCD_DB6: P2.7, U1.67
LCD_DB7: P2.5, U1.69
LCD_E: P2.8, U1.59
LCD_RS: P2.6, U1.76
MCCDA: R48.2, U1.112
MCCK: R68.2, U1.129
MCDA0: R77.2, U1.116
MCDA1: R78.2, U1.118
MCDA2: R22.2, U1.62
MCDA3: R25.2, U1.70
MISO: R101.2, U1.68
MISO_ESP: J16.4, R101.1, U4.6
MOSI: R105.2, U1.42
MOSI_ESP: J16.5, R105.1, U4.7
MOT_RXD: J1.34, R28.1, U1.32, U16.5
MOT_TXD: J1.32, R28.2, U1.37
MUX_0: U1.133, U16.11
MUX_1: J21.6, U1.109, U16.10
MUX_2: U1.86, U16.9
NPCS0: R99.2, U1.64, U12.1
NPCS0_CONN: J16.11, R99.1, U4.10
unnamed: C1.1, C3.1, D1.1, L2.2, R15.1
unnamed: C2.1, D25.1, R107.1, S1.3, S1.4
unnamed: C5.1, U3.4
unnamed: C6.1, C12.1, C125.1, L2.1, R84.1, U3.1
unnamed: C13.1, J22.CE
unnamed: C15.1, U9.18
unnamed: C18.1, R11.2, U1.18
unnamed: C19.1, R12.2, U1.19
unnamed: C20.1, U7.5
unnamed: C20.2, U7.4
unnamed: C21.1, U9.5
unnamed: C21.2, U9.4
unnamed: C26.2, U7.6
unnamed: C27.2, U9.6
unnamed: C28.1, U7.18
unnamed: C30.1, U8.5
unnamed: C30.2, U8.4
unnamed: C31.2, U5.18
unnamed: C36.2, U8.6
unnamed: C38.1, U8.18
unnamed: C39.1, U5.5
unnamed: C39.2, U5.4
unnamed: C44.1, U1.142, X2.3
unnamed: C45.1, U1.141, X2.1
unnamed: C53.1, R10.2, U1.17
unnamed: C57.2, U5.6
unnamed: C59.1, R9.2, U1.16
unnamed: C60.1, R8.2, U1.15
unnamed: C63.1, R7.2, U1.14
unnamed: C65.1, R6.2, U1.12
unnamed: C66.1, R13.2
unnamed: C67.1, L6.2, R13.1, U1.139
unnamed: C81.1, C97.1, C98.1, L1.1, L3.2, R87.1
unnamed: C81.2, R87.2, R88.1, U3.5
unnamed: C84.1, R50.2, U1.24
unnamed: C92.1, U6.18
unnamed: C93.1, U6.4
unnamed: C93.2, U6.5
unnamed: C96.1, U3.11
unnamed: C96.2, D2.1, L1.2, U3.12
unnamed: C100.2, U6.6
unnamed: C105.1, J17.2, Ju2.2, U10.8
unnamed: C105.2, J17.3, Ju1.1, R40.2, U10.7
unnamed: C112.2, R90.1, U6.12
unnamed: C124.2, R93.1, U6.9
unnamed: C126.1, J18.2, Ju3.1, U13.8
unnamed: C126.2, J18.3, Ju4.1, R34.2, U13.7
unnamed: C127.2, R27.2, U7.12
unnamed: C128.2, R45.2, U5.12
unnamed: C129.2, R32.2, U7.9
unnamed: C130.2, R41.2, U5.9
unnamed: C131.2, R39.2, U8.12
unnamed: C132.2, R44.2, U8.9
unnamed: C133.2, R29.2, U9.12
unnamed: C134.2, R33.2, U9.9
unnamed: D2.2, R85.2, R86.2, U3.8
unnamed: D3.2, R1.1
unnamed: D7.1, R67.1
unnamed: D9.1, R69.1
unnamed: D10.1, R70.1
unnamed: D11.1, R71.1
unnamed: D12.1, R72.1
unnamed: D14.2, JP10.2
unnamed: D15.2, R55.1
unnamed: D16.2, R60.1
unnamed: D17.2, R61.1
unnamed: D19.1, R96.1
unnamed: D20.1, R98.1
unnamed: F2.2, J3.3
unnamed: J15.1, R22.1, R73.1
unnamed: J15.2, R25.1, R74.1
unnamed: J15.3, R48.1, R63.1
unnamed: J15.5, R68.1
unnamed: J15.7, R75.1, R77.1
unnamed: J15.8, R76.1, R78.1
unnamed: J15.9, R64.1, R79.1
unnamed: J17.1, Ju2.1, U10.9
unnamed: J17.4, Ju1.2, U10.5, U10.6
unnamed: J18.1, Ju3.2, U13.9
unnamed: J18.4, Ju4.2, U13.5, U13.6
unnamed: J22.2, R3.1
unnamed: J22.3, R2.1
unnamed: J7.1, J36.2
unnamed: J7.3, J36.4
unnamed: JP9.2, U3.10
unnamed: L8.2, U7.10
unnamed: L9.2, U7.8
unnamed: L10.2, U7.11
unnamed: L11.2, U7.13
unnamed: L12.2, U8.10
unnamed: L13.2, U8.8
unnamed: L14.2, U8.11
unnamed: L15.2, U8.13
unnamed: L16.2, U9.10
unnamed: L17.2, U9.8
unnamed: L18.2, U9.11
unnamed: L19.2, U9.13
unnamed: L20.2, U5.10
unnamed: L21.2, U5.8
unnamed: L22.2, U5.11
unnamed: L23.2, U5.13
unnamed: L24.2, U6.10
unnamed: L25.2, U6.8
unnamed: L26.2, U6.11
unnamed: L27.2, U6.13
unnamed: R4.1, R5.1, U4.1
unnamed: R14.1, TR7.G
unnamed: R20.1, TR2.G
unnamed: R23.1, TR4.G
unnamed: R30.1, R34.1, U13.1, U13.2
unnamed: R30.2, U13.3, U13.4
unnamed: R38.1, R40.1, U10.1, U10.2
unnamed: R38.2, U10.3, U10.4
unnamed: R42.1, TR5.G
unnamed: R43.1, TR9.G
unnamed: R66.1, TR1.G
unnamed: R82.2, U4.13, U12.5
unnamed: R84.2, U3.3
unnamed: R97.1, TR8.G
unnamed: U11.1, U11.6, U11.9, U11.12
PB6/TMS: J1.29, J21.2, R52.2, U1.79
PB7/TCK: J21.4, R49.2, R83.2, U1.89
PS_ON: R14.2, R54.1, U1.106
PS_ON_IN: J20.2, TR7.D
PWR_FAIL_DET1: C80.1, R15.2, R16.1, U1.31
PWR_FAIL_DET2: C79.1, R80.2, R81.1, U1.41
RESET: D25.2, J21.10, R106.1, U1.83
RESET_EXT: J1.44, R107.2
SAM_TFR_RDY: R82.1, U1.34, U12.3
SD_CD: R79.2, U1.122
SPCK: R100.2, U1.51
SPCK_ESP: J16.3, R100.1, U4.5
SPI0_CS0: P1.3, U1.130
SPI0_CS1: J37.3, U1.26
SPI0_CS2: J37.1, U1.111
SPI0_MISO: J1.49, J37.6, P1.6, U1.21
SPI0_MOSI: J1.48, J37.5, P1.5, U1.20
SPI0_SCK: J1.47, J37.4, P1.4, U1.144
TEMP_CS1: U1.84, U10.13
TEMP_CS2: J21.8, R36.2, U1.105, U13.13
TEMP_MISO: U1.103, U10.14, U13.14
TEMP_MOSI: U1.90, U10.11, U13.11
TEMP_SCK: U1.46, U10.12, U13.12
THERMISTOR0: J5.2, R12.1, R21.1
THERMISTOR1: J12.2, R11.1, R19.1
THERMISTOR2: J14.2, R10.1, R53.1
THERMISTOR3: J1.35, R9.1
THERMISTOR4: J1.36, R8.1
THERMISTOR5: J1.37, R7.1
THERMISTOR6: J1.38, R6.1
THERMISTOR7: J1.39, R50.1
TWCK0: J1.46, U1.77
TWD0: J1.45, U1.91
URXD0: J30.3, P1.9, U1.75
URXD1: R102.2, U1.73
URXD1_CONN: J16.15, J39.3, R102.1, U4.16
USB_PWR_MON: C82.1, R31.1, R37.2, U1.124
UTXD0: J30.4, P1.10, U1.66
UTXD1: R103.2, U1.114
UTXD1_CONN: C83.1, J16.14, J39.5, R103.1, U4.15
VBUS: D3.1, D13.1, J22.1, R37.1
VSSA: F1.1, J1.40, J5.1, J12.1, J14.1, R83.1
V_BED: C91.1, F4.2, J4.2, R65.2
V_FAN: D8.1, D18.1, D21.1, J2.1, J3.2, J24.1, J25.1, J29.1, J31.1
V_FUSED: C22.1, C23.1, C24.1, C25.1, C26.1, C27.1, C32.1, C33.1, C35.1, C36.1, C56.1, C57.1, C75.1, C76.1, C77.1, C78.1, C94.1, C95.1, C100.1, C101.1, C102.1, D1.2, F3.2, J11.1, J13.1, R67.2, R80.1, R98.2, U5.7, U5.14, U6.7, U6.14, U7.7, U7.14, U8.7, U8.14, U9.7, U9.14
V_IN: D15.1, F2.1, F3.1, F4.1, J23.1
X_DIR: J40.1, U1.98, U7.23
X_MOT_1A: C88.2, J9.2, L8.1, VR1.1, VR3.1
X_MOT_1B: C85.2, J9.1, L10.1, VR4.1, VR6.1
X_MOT_2A: C107.1, J9.3, L9.1, VR2.2, VR3.2
X_MOT_2B: C113.1, J9.4, L11.1, VR5.2, VR6.2
X_STEP: J41.1, U1.121, U7.25
X_STOP: C40.1, D23.1, R56.1, U1.97
X_STOP_CONN: D12.2, J33.1, R56.2
X_UART: J27.1, R26.1, U7.20, U16.2
Y_DIR: J44.1, U1.92, U8.23
Y_MOT_1A: C89.2, J8.2, L12.1, VR7.1, VR9.1
Y_MOT_1B: C86.2, J8.1, L14.1, VR10.1, VR12.1
Y_MOT_2A: C108.1, J8.3, L13.1, VR8.2, VR9.2
Y_MOT_2B: C114.1, J8.4, L15.1, VR11.2, VR12.2
Y_STEP: J45.1, U1.119, U8.25
Y_STOP: C41.1, D22.1, R57.1, U1.93
Y_STOP_CONN: D9.2, J32.1, R57.2
Y_UART: J42.1, R46.1, U8.20, U16.3
Z_DIR: J48.1, U1.88, U9.23
Z_MOT_1A: C106.2, J7.2, L16.1, VR13.1, VR15.1
Z_MOT_1B: C87.2, J36.1, L18.1, VR16.1, VR18.1
Z_MOT_2A: C109.1, J36.3, L17.1, VR14.2, VR15.2
Z_MOT_2B: C115.1, J7.4, L19.1, VR17.2, VR18.2
Z_PROBE_IN: J28.1, R62.2
Z_PROBE_MCU: C90.1, D24.2, R62.1, U1.38
Z_PROBE_MOD: J28.3, U1.39
Z_STEP: J49.1, U1.113, U9.25
Z_STOP: C42.1, D22.2, R58.1, U1.108
Z_STOP_CONN: D10.2, J19.1, R58.2
Z_UART: J46.1, R35.1, U9.20, U16.4

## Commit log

2018-10-30 cleaned up files
    [Comms.sch, Duet0.3.brd, Duet0.3.sch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]
2018-10-30 fixed DRC
    FIxed DRC errors.
    [DuetWifi.kicad_pcb]
2018-11-01 added bom list.
    parts are spread among both vendors. you need the parts from both lists.
    [bom - farnell.ods, bom - tme.ods]
